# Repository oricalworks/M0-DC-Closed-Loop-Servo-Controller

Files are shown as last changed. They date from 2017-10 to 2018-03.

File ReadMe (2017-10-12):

Circuit Pro Industries M0 DC Closed Loop Servo

   read a rotary encoder with interrupts
   Encoder hooked up with common to GROUND,
   encoder0PinA to pin 2, encoder0PinB to pin 4 (or pin 3 see below)
   it doesn't matter which encoder pin you use for A or B 
   
   is possible to change PID costants by sending on SerialUSB interfaces the values separated by ',' in this order: KP,KD,KI
   example: 5.2,3.1,0 so we have  KP=5.2 KD=3.1 KI=0 is only for testing purposes, but i will leave this function with eeprom storage

*/ 
/*   -----------------To Do-----------------
 *
 *    Come up with offical name!!!!!
 *    Implement code for physical EEPROM for V2 Board (Chip:24LC256 ADDRESS:0x50) (32Kb Storage) (I2c on SDA and SCL)
 *    PID Auto Tune
 *    Error Reporting
 *    Force sensing
 *    Host Communincation
 *    Performance Reporting and Info for Osiliscope
 *    Switchless Homing(force sensing)
 *    Master and Slave Mirroring
 *    Configurable Limits
 *    Create Host Software
 *    Implement Unit linking
 *    Implement Wire communication (Serial I2C)
 *    Complete data sheet and usage guide.
 *    
*/

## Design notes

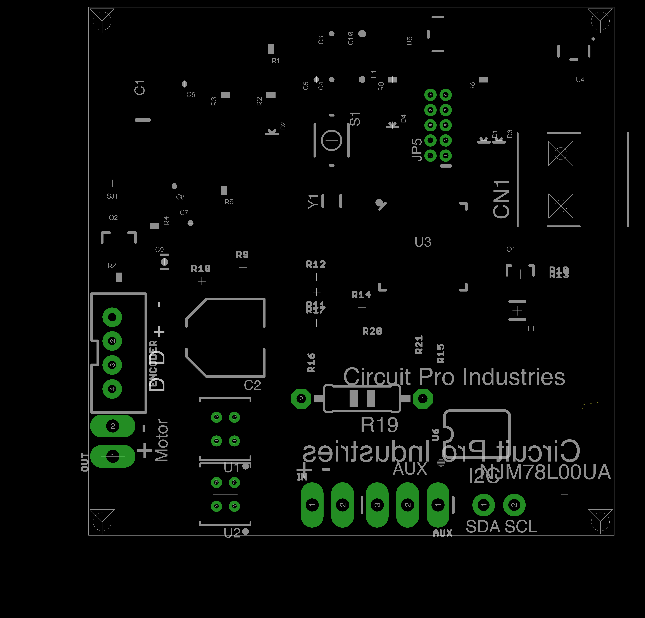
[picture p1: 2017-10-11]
Base image Ref.png

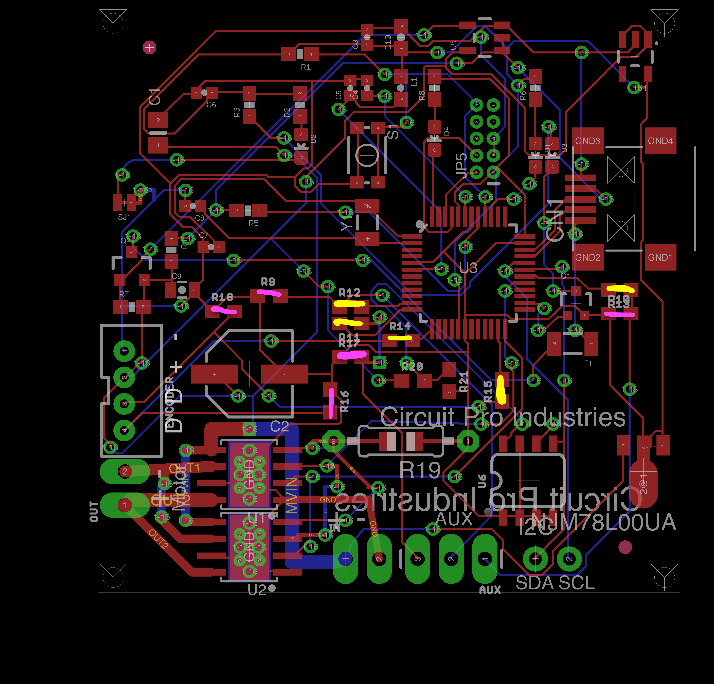
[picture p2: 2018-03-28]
Board Refrence.png

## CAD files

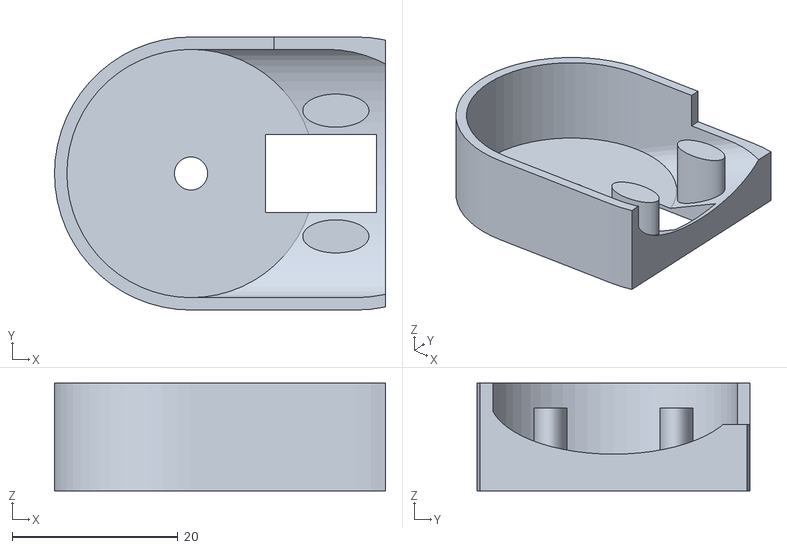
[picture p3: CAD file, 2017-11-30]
encoder.stl
40.0 x 33.0 x 13.0

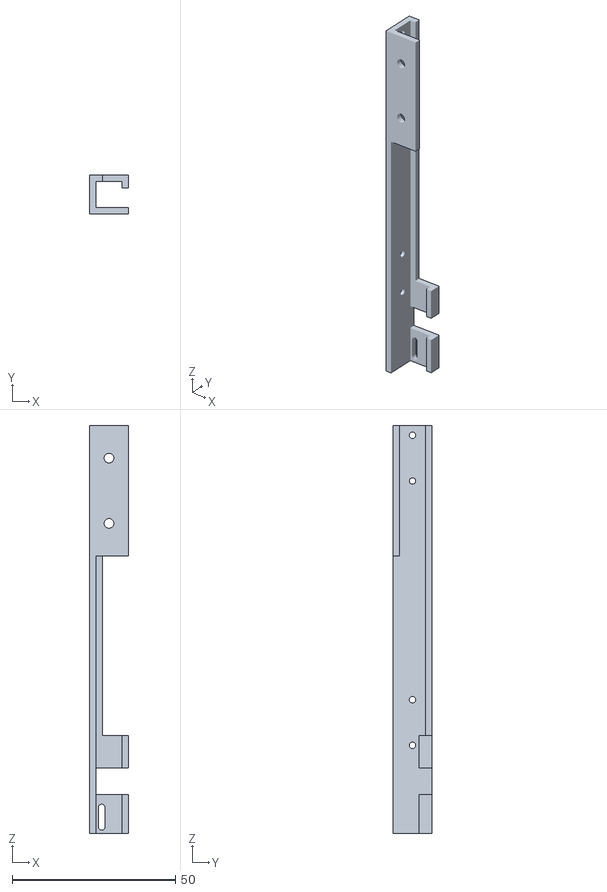
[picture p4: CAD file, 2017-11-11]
Feeder/Part1.stl
12.0 x 12.0 x 125.0

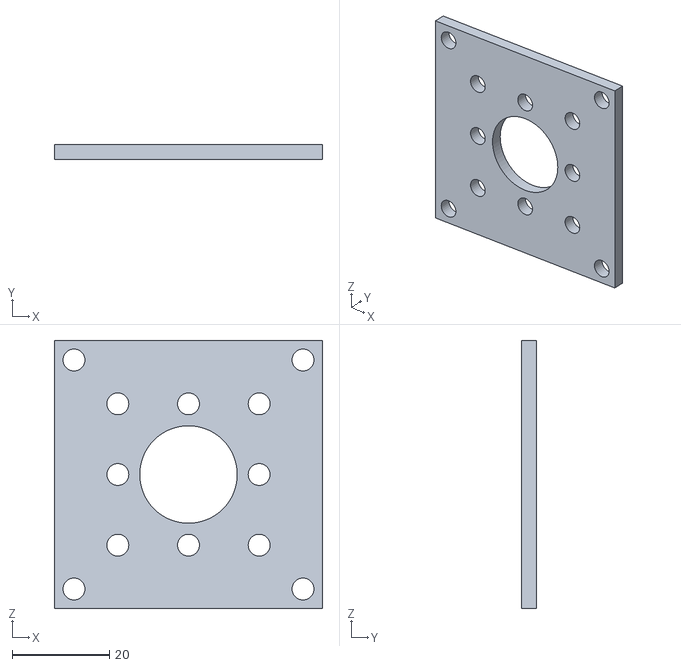
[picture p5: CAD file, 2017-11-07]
Servo Hardware/NEMA 23 to 775 motor plate.stl
55.0 x 3.00 x 55.0

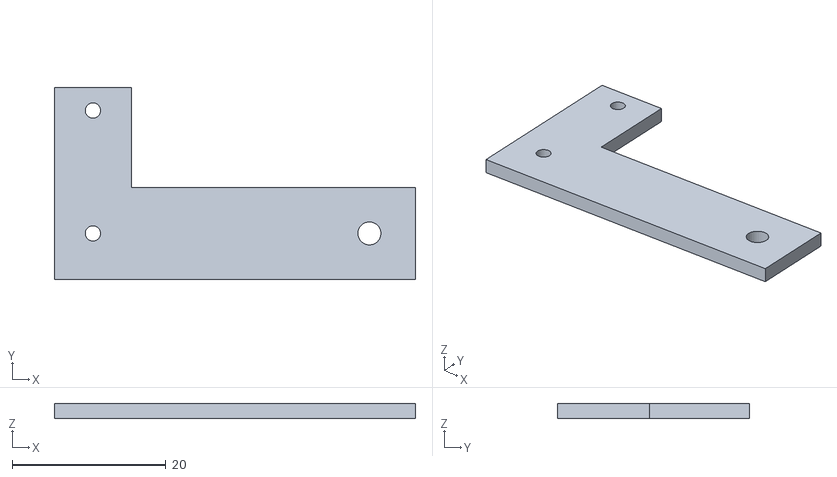
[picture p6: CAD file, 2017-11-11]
Feeder/Part4.stl
47.0 x 25.0 x 2.00

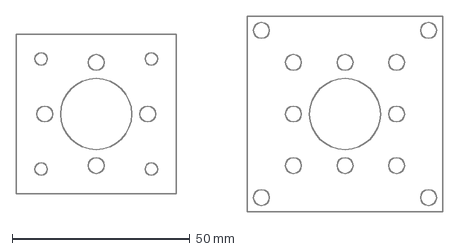
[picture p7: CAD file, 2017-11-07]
Servo Hardware/775 Motor Adapter Plate NEMA 17 & 23 .dxf
120.0 x 55.0 mm

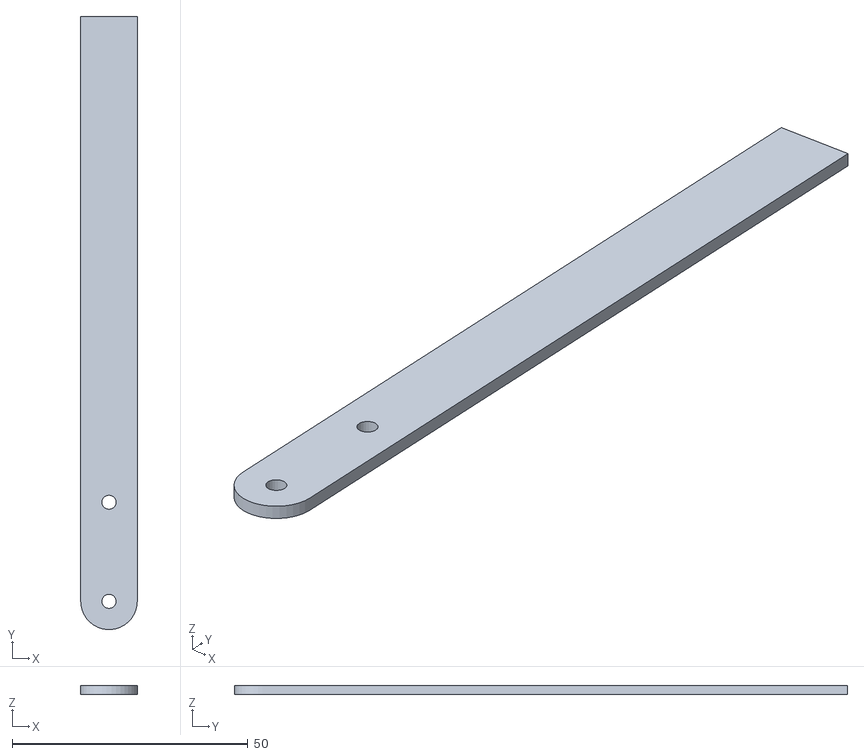
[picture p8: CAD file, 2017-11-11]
Feeder/Part5.stl
12.0 x 130.0 x 2.00

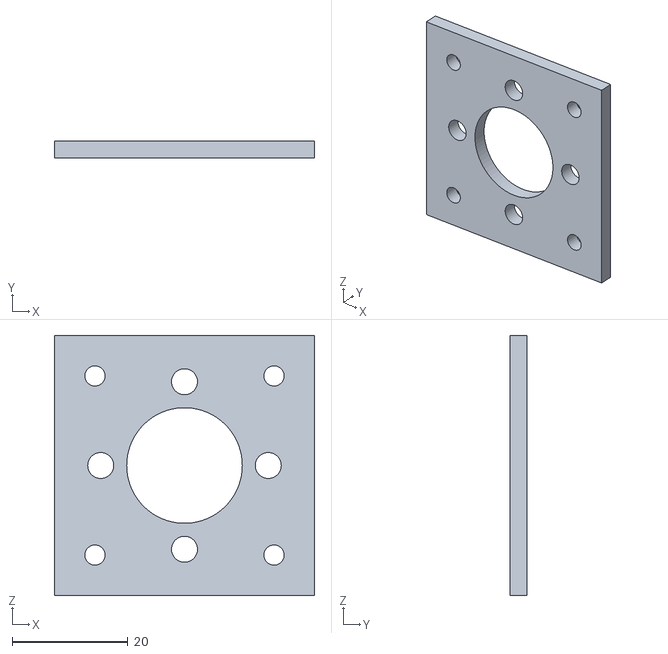
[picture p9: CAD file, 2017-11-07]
Servo Hardware/NEMA17 to 775 motor plate.stl
45.0 x 3.00 x 45.0

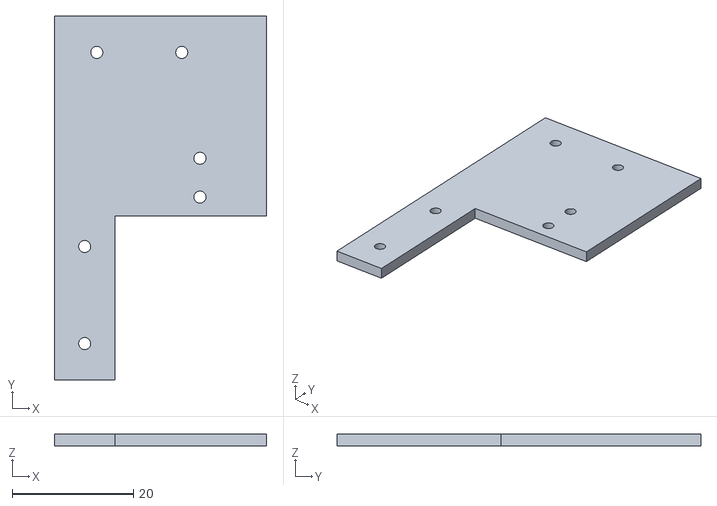
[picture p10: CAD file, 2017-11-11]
Feeder/Part3.stl
35.0 x 60.0 x 2.00

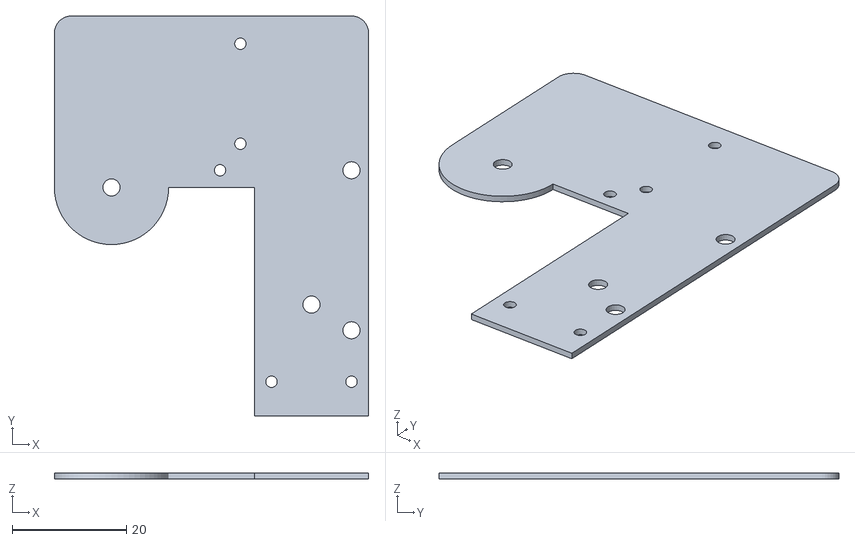
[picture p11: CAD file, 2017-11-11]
Feeder/part 8.stl
55.0 x 70.0 x 1.00

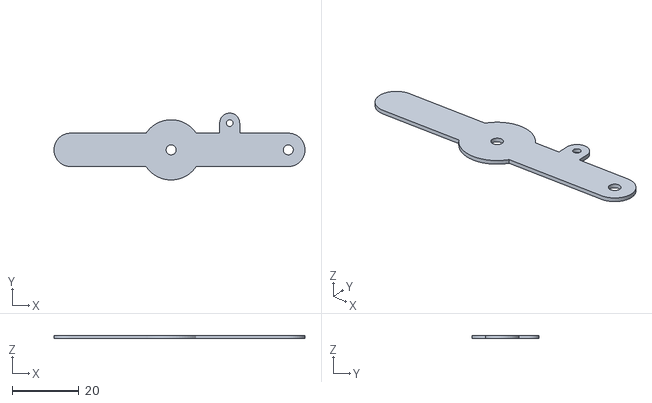
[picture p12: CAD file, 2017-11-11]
Feeder/Part9.stl
75.0 x 20.0 x 1.00

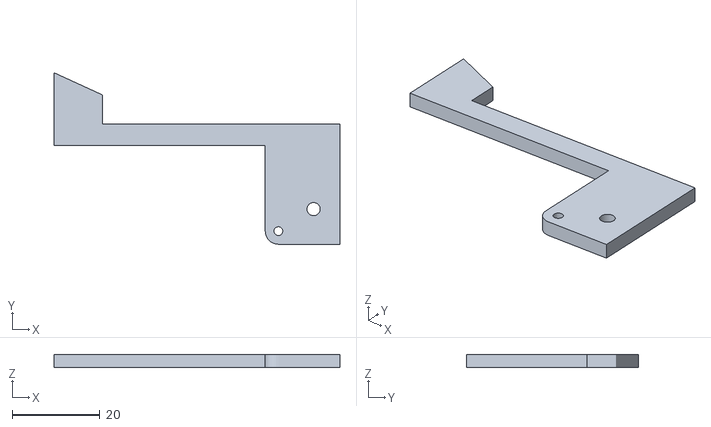
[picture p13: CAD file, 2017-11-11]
Feeder/Part6.stl
65.0 x 39.0 x 3.00

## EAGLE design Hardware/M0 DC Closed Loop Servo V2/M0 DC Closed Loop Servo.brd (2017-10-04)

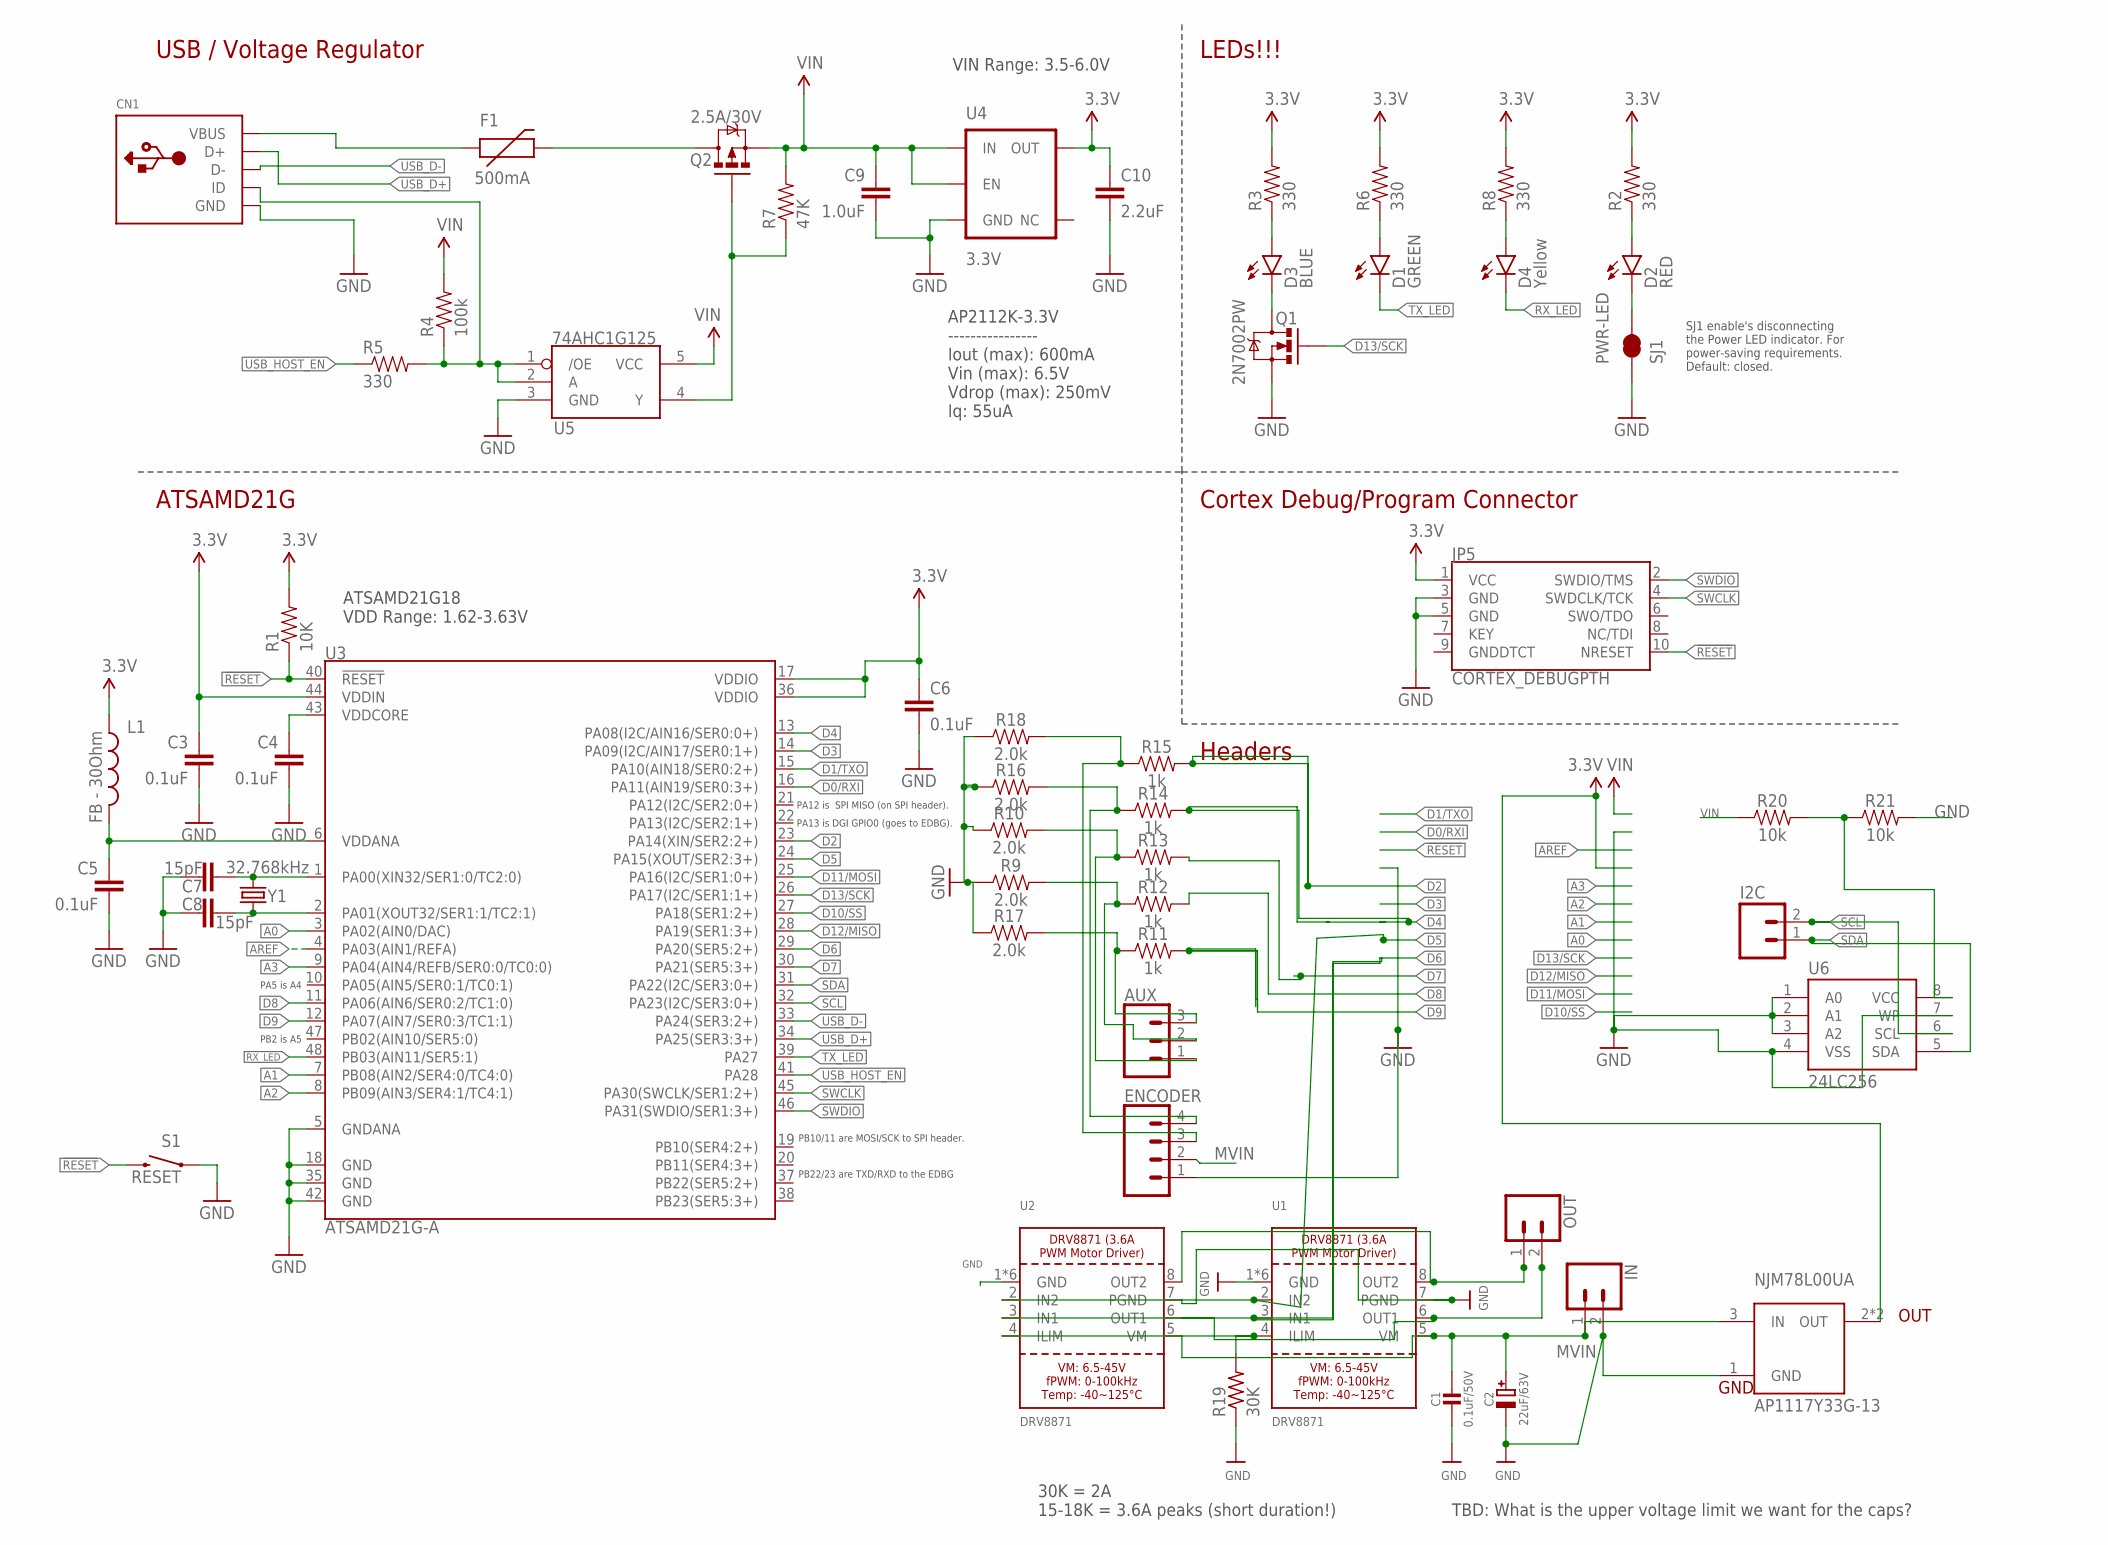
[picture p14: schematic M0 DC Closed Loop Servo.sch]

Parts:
AUX: CONN_03LONGPADS; 1X03_LONGPADS
C1: 0.1uF/50V; 0805-NO
C2: 22uF/63V; PANASONIC_D
C3, C4, C5, C6: 0.1uF; 0402-CAP
C7, C8: 15pF; 0402-CAP
C9: 1.0uF; 0805-CAP
C10: 2.2uF; 0603-CAP
CN1: USBMINIB; USB-MINIB
D1: GREEN; LED-0603
D2: RED; LED-0603
D3: BLUE; LED-0603
D4: Yellow; LED-0603
ENCODER: CONN_04JST-PTH-VERT; JST-4-PTH-VERT
F1: 500mA; PTC-1206
I2C: M021X02_NO_SILK; 1X02_NO_SILK@1
IN: CONN_02PTH3; 1X02_LONGPADS
JP5: CORTEX_DEBUGPTH; 2X5-PTH-1.27MM
L1: FB - 30Ohm; 0603
NJM78L00UA: AP1117Y33G-13; SOT89
OUT: CONN_02PTH3; 1X02_LONGPADS
Q1: 2N7002PW; SOT323
Q2: 2.5A/30V; SOT23-3
R1: 10K; 0603-RES
R2, R3, R5, R6, R8: 330; 0603-RES
R4: 100k; 0603-RES
R7: 47K; 0603-RES
R9, R10, R16, R17, R18: 2.0k; 0603
R11, R12, R13, R14, R15: 1k; 0603
R19: 30K; 0805-THM
R20, R21: 10k; 0603
S1: RESET; TACTILE_SWITCH_SMD_4.6X2.8MM
SJ1: PWR-LED; PAD-JUMPER-2-NC_BY_TRACE_NO_SILK
U1, U2: DRV8871; HSOP8
U3: ATSAMD21G-A; TQFP-48
U4: 3.3V; SOT23-5
U5: 74AHC1G125; SOT23-5
U6: 24LC256; SO08
Y1: 32.768kHz; CRYSTAL-SMD-3.2X1.5MM

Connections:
3.3V: C3.1, C6.1, C10.1, JP5.1 (VCC), L1.1, NJM78L00UA.2 (OUT), NJM78L00UA.2@1 (OUT), R1.2, R2.2, R3.2, R6.2, R8.2, U3.17 (VDDIO), U3.36 (VDDIO), U3.44 (VDDIN), U4.5 (OUT)
!RESET: JP5.10 (NRESET), R1.1, S1.3 (2), S1.4 (2), U3.40 (!RESET!)
A0: U3.3 (PA02(AIN0/DAC))
A1: U3.7 (PB08(AIN2/SER4:0/TC4:0))
A2: U3.8 (PB09(AIN3/SER4:1/TC4:1))
A3: U3.9 (PA04(AIN4/REFB/SER0:0/TC0:0))
AREF: U3.4 (PA03(AIN1/REFA))
D0/RXI: U3.16 (PA11(AIN19/SER0:3+))
D1/TXO: U3.15 (PA10(AIN18/SER0:2+))
D2: R15.2, U3.23 (PA14(XIN/SER2:2+))
D3: U3.14 (PA09(I2C/AIN17/SER0:1+))
D4: R14.2, U3.13 (PA08(I2C/AIN16/SER0:0+))
D5: U1.2 (IN2), U2.2 (IN2), U3.24 (PA15(XOUT/SER2:3+))
D6: U1.3 (IN1), U2.3 (IN1), U3.29 (PA20(SER5:2+))
D7: R13.2, U3.30 (PA21(SER5:3+))
D8: R12.2, U3.11 (PA06(AIN6/SER0:2/TC1:0))
D9: R11.2, U3.12 (PA07(AIN7/SER0:3/TC1:1))
D10/SS: U3.27 (PA18(SER1:2+))
D11/MOSI: U3.25 (PA16(I2C/SER1:0+))
D12/MISO: U3.28 (PA19(SER1:3+))
D13/SCK: Q1.1 (G), U3.26 (PA17(I2C/SER1:1+))
ENCODER: ENCODER.3, R15.1, R18.2
GND: C1.2, C2.-, C3.2, C4.2, C5.2, C6.2, C7.1, C8.2, C9.2, C10.2, CN1.GND, ENCODER.1, IN.2, JP5.3 (GND), JP5.5 (GND), NJM78L00UA.1 (GND), Q1.2 (S), R9.1, R10.1, R16.1, R17.1, R18.1, R19.1, R21.2, S1.1, S1.2 (1), SJ1.1, U1.1 (GND), U1.7 (PGND), U1.GND, U1.P$1 (GND), U1.P$2 (GND), U1.P$3 (GND), U1.P$4 (GND), U2.1 (GND), U2.7 (PGND), U2.GND, U2.P$1 (GND), U2.P$2 (GND), U2.P$3 (GND), U2.P$4 (GND), U3.5 (GNDANA), U3.18 (GND), U3.35 (GND), U3.42 (GND), U4.2 (GND), U5.3 (GND), U6.1 (A0), U6.2 (A1), U6.3 (A2), U6.4 (VSS), U6.7 (WP)
MVIN: C1.1, C2.+, ENCODER.2, IN.1, NJM78L00UA.3 (IN), U1.5 (VM), U2.5 (VM)
unnamed: CN1.VBUS, F1.1
unnamed: C7.2, U3.1 (PA00(XIN32/SER1:0/TC2:0)), Y1.P$2 (2)
unnamed: D3.C, Q1.3 (D)
unnamed: C8.1, U3.2 (PA01(XOUT32/SER1:1/TC2:1)), Y1.P$1 (1)
unnamed: D2.A, R2.1
unnamed: D3.A, R3.1
unnamed: F1.2, Q2.3 (D)
unnamed: CN1.ID, R4.1, R5.2, U5.1 (/OE), U5.2 (A)
unnamed: Q2.1 (G), R7.1, U5.4 (Y)
unnamed: D1.A, R6.1
unnamed: D4.A, R8.1
unnamed: D2.C, SJ1.2
unnamed: AUX.3, R11.1, R17.2
unnamed: R20.2, R21.1, U6.8 (VCC)
unnamed: AUX.2, R9.2, R12.1
unnamed: AUX.1, R10.2, R13.1
unnamed: ENCODER.4, R14.1, R16.2
unnamed: R19.2, U1.4 (ILIM), U2.4 (ILIM)
OUT1: OUT.2, U1.6 (OUT1), U2.6 (OUT1)
OUT2: OUT.1, U1.8 (OUT2), U2.8 (OUT2)
RX_LED: D4.C, U3.48 (PB03(AIN11/SER5:1))
SCL: I2C.2, U3.32 (PA23(I2C/SER3:0+)), U6.6 (SCL)
SDA: I2C.1, U3.31 (PA22(I2C/SER3:0+)), U6.5 (SDA)
SWCLK: JP5.4 (SWDCLK/TCK), U3.45 (PA30(SWCLK/SER1:2+))
SWDIO: JP5.2 (SWDIO/TMS), U3.46 (PA31(SWDIO/SER1:3+))
TX_LED: D1.C, U3.39 (PA27)
USB_D+: CN1.D+, U3.34 (PA25(SER3:3+))
USB_D-: CN1.D-, U3.33 (PA24(SER3:2+))
USB_HOST_EN: R5.1, U3.41 (PA28)
VDDANA: C5.1, L1.2, U3.6 (VDDANA)
VDDCORE: C4.1, U3.43 (VDDCORE)
VIN: C9.1, Q2.2 (S), R4.2, R7.2, R20.1, U4.1 (IN), U4.3 (EN), U5.5 (VCC)

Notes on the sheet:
PB22/23 are TXD/RXD to the EDBG
PB10/11 are MOSI/SCK to SPI header.
PA12 is SPI MISO (on SPI header).
PA13 is DGI GPIO0 (goes to EDBG).
PA5 is A4
PB2 is A5
USB / Voltage Regulator
LEDs!!!
Cortex Debug/Program Connector
Headers
ATSAMD21G
ATSAMD21G18 VDD Range: 1.62-3.63V
SJ1 enable's disconnecting the Power LED indicator. For power-saving requirements. Default: closed.
VIN Range: 3.5-6.0V
AP2112K-3.3V ---------------- Iout (max): 600mA Vin (max): 6.5V Vdrop (max): 250mV Iq: 55uA
TBD: What is the upper voltage limit we want for the caps?
30K = 2A 15-18K = 3.6A peaks (short duration!)
GND
OUT

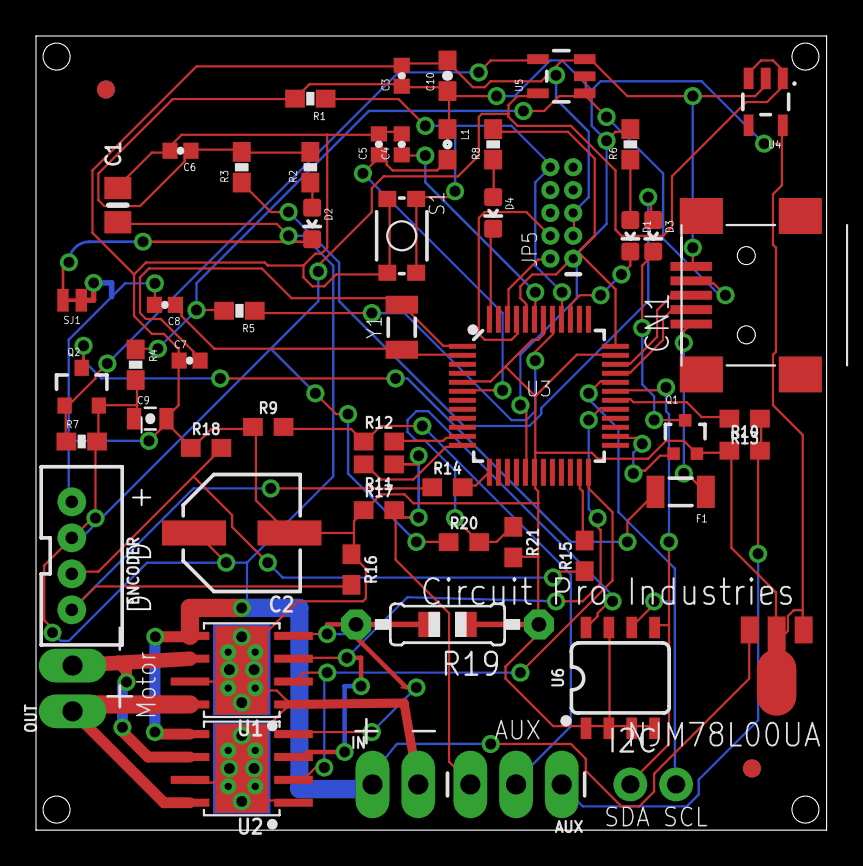
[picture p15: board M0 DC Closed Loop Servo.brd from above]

Board: 2 copper layers, 43.9 x 44.1 mm, 58 parts (0 on the bottom side), 45 nets.

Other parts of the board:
U$7, U$8: CIRCLE-1MM-3R

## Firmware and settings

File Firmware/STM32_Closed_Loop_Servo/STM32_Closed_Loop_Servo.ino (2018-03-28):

/*
   
   https://github.com/JChristensen/extEEPROM - EEPROM LIBRARY
   
   read a rotary encoder with interrupts
   Encoder hooked up with common to GROUND,
   encoder0PinA to pin 2, encoder0PinB to pin 4 (or pin 3 see below)
   it doesn't matter which encoder pin you use for A or B 
   
   is possible to change PID costants by sending on SerialUSB interfaces the values separated by ',' in this order: KP,KD,KI
   example: 5.2,3.1,0 so we have  KP=5.2 KD=3.1 KI=0 is only for testing purposes, but i will leave this function with eeprom storage

*/ 
/*   -----------------To Do-----------------
 *    Implement code for physical EEPROM for V2 Board (Chip:24LC256 ADDRESS:0x50) (32Kb Storage) (I2c on SDA and SCL)
 *    PID Auto-Tune
 *    Error Reporting
 *    Force sensing
 *    Host Communincation
 *    Performance Reporting and Info for Osiliscope
 *    Switchless Homing(force sensing)
 *    Master and Slave Mirroring
 *    Configurable Limits
 *    Create Host Software
 *    
*/

// Set the pins used



// blink out an error code



//Hardware setup
#define encoder0PinA  2
#define encoder0PinB  3

#define SpeedPin     9
#define DirectionPin 8

//Step & Dir Interface 
#define STEP_PIN              3
#define DIR_PIN               12
#define ENABLE_PIN            13
// HS END

volatile long encoder0Pos = 0;

long target = 0;
long target1 = 0;
int amp=212;
//correction = Kp * error + Kd * (error - prevError) + kI * (sum of errors)
//PID controller constants
float KP = 6.0 ; //position multiplier (gain) 2.25
float KI = 0.1; // Intergral multiplier (gain) .25
float KD = 1.3; // derivative multiplier (gain) 1.0

int lastError = 0;
int sumError = 0;

//Integral term min/max (random value and not yet tested/verified)
int iMax = 100;
int iMin = 0;

long previousTarget = 0;
long previousMillis = 0;        // will store last time LED was updated
long interval = 5;           // interval at which to blink (milliseconds)

//for motor control ramps 1.4
bool newStep = false;
bool oldStep = false;
bool dir = false;

void setup() { 
  


  pinMode(encoder0PinA, INPUT_PULLUP); 
  pinMode(encoder0PinB, INPUT_PULLUP);  
  
  pinMode(DirectionPin, OUTPUT); 
  pinMode(SpeedPin, OUTPUT);
  
  //ramps 1.4 motor control
    pinMode(STEP_PIN, INPUT);
    pinMode(DIR_PIN, INPUT);

  attachInterrupt(2, doEncoderMotor0, CHANGE);  // encoder pin on interrupt 0 - pin 2
  attachInterrupt(3, countStep, RISING);  //on pin 3
  SerialUSB.begin(15200);
  SerialUSB.println("start");               

} 

void loop(){
  
  while (SerialUSB.available() > 0) {
    KP = SerialUSB.read();
    KD = SerialUSB.read();
    KI = SerialUSB.read();
    
    
    SerialUSB.println(KP);
    SerialUSB.println(KD);
    SerialUSB.println(KI);
}
  
  if(millis() - previousTarget > 500){ //enable this code only for test purposes
  SerialUSB.print(encoder0Pos);
  SerialUSB.print(',');
  SerialUSB.println(target1);
  previousTarget=millis();
  }
        
  target = target1;
  docalc();
}

void docalc() {
  
  if (millis() - previousMillis > interval) 
  {
    previousMillis = millis();   // remember the last time we blinked the LED
    
    long error = encoder0Pos - target ; // find the error term of current position - target    
    
    //generalized PID formula
    //correction = Kp * error + Kd * (error - prevError) + kI * (sum of errors)
    long ms = KP * error + KD * (error - lastError) +KI * (sumError);
       
    lastError = error;    
    sumError += error;
    
    //scale the sum for the integral term
    if(sumError > iMax) {
      sumError = iMax;
    } else if(sumError < iMin){
      sumError = iMin;
    }
    
    if(ms > 0){
      digitalWrite ( DirectionPin ,HIGH );      
    }
    if(ms < 0){
      digitalWrite ( DirectionPin , LOW );     
      ms = -1 * ms;
    }

    int motorspeed = map(ms,0,amp,0,255);
   if( motorspeed >= 255) motorspeed=255;
    //analogWrite ( SpeedPin, (255 - motorSpeed) );
    analogWrite ( SpeedPin,  motorspeed );
    //SerialUSB.print ( ms );
    //SerialUSB.print ( ',' );
    //SerialUSB.println ( motorspeed );
  }  
}

void doEncoderMotor0(){
  if (digitalRead(encoder0PinA) == HIGH) {   // found a low-to-high on channel A
    if (digitalRead(encoder0PinB) == LOW) {  // check channel B to see which way
                                             // encoder is turning
      encoder0Pos = encoder0Pos - 1;         // CCW
    } 
    else {
      encoder0Pos = encoder0Pos + 1;         // CW
    }
  }
  else                                        // found a high-to-low on channel A
  { 
    if (digitalRead(encoder0PinB) == LOW) {   // check channel B to see which way
                                              // encoder is turning  
      encoder0Pos = encoder0Pos + 1;          // CW
    } 
    else {
      encoder0Pos = encoder0Pos - 1;          // CCW
    }

  }
 
}

void countStep(){
  dir = digitalRead(DIR_PIN);
            if (dir) target1++;
            else target1--;
}

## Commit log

2017-10-03 Added Firmware and Hardware
    Added Firmware and Hardware
    [M0 DC Closed Loop Servo.brd, M0 DC Closed Loop Servo.sch]
2017-10-04 V2 Board Update
2017-10-04 Added Thermal Vias and Pads
    [M0 DC Closed Loop Servo.brd]
2017-10-12 Updated Data Sheet
    Need To come Up with and official name to for the board rather than
    SPEC name
2017-11-07 Mega Update
    [775 Motor Adapter Plate NEMA 17 & 23 .dxf, NEMA 23 to 775 motor plate.stl, NEMA17 to 775 motor plate.stl]
2017-11-11 fixed trace collision
    [M0 DC Closed Loop Servo.brd, Part1.stl, Part3.stl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]
2017-11-30 Board Redesign, Rework, and Overhaul to V2
    Board Redesign, Rework, and Overhaul to V2
    [M0 DC Closed Loop Servo.brd, M0 DC Closed Loop Servo.sch, encoder.stl]
2017-12-01 Board Clean UP
    [M0 DC Closed Loop Servo.brd, M0 DC Closed Loop Servo.sch]
2017-12-01 COMPLETE OVER HULL
    [M0 DC Closed Loop Servo.brd, M0 DC Closed Loop Servo.sch]

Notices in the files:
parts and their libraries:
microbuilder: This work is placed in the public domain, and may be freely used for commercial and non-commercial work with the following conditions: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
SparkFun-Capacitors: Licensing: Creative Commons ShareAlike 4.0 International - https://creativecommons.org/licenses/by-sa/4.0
